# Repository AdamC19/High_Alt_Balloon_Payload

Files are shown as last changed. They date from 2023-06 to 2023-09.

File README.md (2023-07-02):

# High-Altitude Balloon Payload

These are the source files for my high-altitude balloon payload. 

Read more about this project and its development [on my website](http://acordingley.us/ke8itf/).

The primary goals of the payload are:
* Make measurements and collect data: 
    * GPS Location
    * Barometric pressure (second determination of altitude)
    * Temperature.
* Telemeter the data via the Amatuer Radio 2m band (144.39MHz).
* Log the data to non-volatile storage.
* Powered from NiMH batteries.

The primary goal of the real-time telemetry is to be able to receive GPS coordinates so that we can track the balloon and hopefully chase it and find it more easily. The payload will also include a self-contained camera to take pictures. 

## Hardware Block Diagrams
### Logical Overview
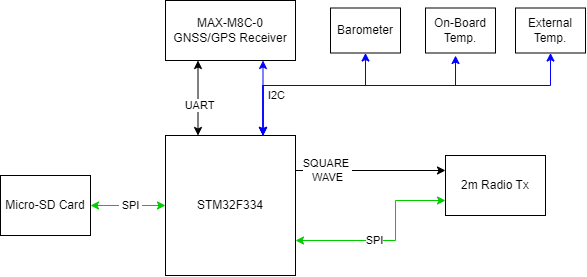
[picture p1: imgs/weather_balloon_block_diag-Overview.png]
High Altitude Balloon Payload Overview Block Diagram


### Power Architecture
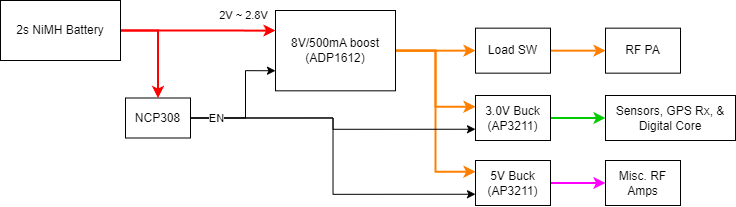
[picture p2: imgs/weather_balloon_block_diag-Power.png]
High Altitude Balloon Payload Power Block Diagram


### 2m Radio Transmitter
High Altitude Balloon Payload Radio Block Diagram

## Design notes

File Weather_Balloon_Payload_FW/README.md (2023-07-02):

# Payload Firmware

The boilerplate code was generated using STM32CubeMX. 

You can build using make, and it's convenient to use Visual Studio Code with the stm32-for-vscode extension.

## SD Card Driver

Big thanks to projects by kiwih for providing the boilerplate [SD card SPI driver code](https://01001000.xyz/2020-08-09-Tutorial-STM32CubeIDE-SD-card/).

The FAT filesystem middleware was provided by ST via STM32CubeMX.

You can configure the radio by including a file named `config.txt` on the SD card. I've included an example of such a file.

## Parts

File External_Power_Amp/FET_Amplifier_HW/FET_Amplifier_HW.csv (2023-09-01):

Source: | C:\Users\cordi\OneDrive\Documents\GitHub\Weather_Balloon\External_Power_Amp\FET_Amplifier_HW\FET_Amplifier_HW.kicad_sch
Date: | 7/29/2023 1:38:26 AM
Tool: | Eeschema 7.0.1
Generator: | C:\Program Files\KiCad\7.0\bin\scripting\plugins/bom_csv_grouped_by_value.py
Component Count: | 109
Collated Components:
Item | Qty | Reference(s) | Value | LibPart | Footprint | Datasheet | DNP | Current Rating | Description | JLCPCB Part # | MFG | MFG_PN | Manufacturer | Mfr Part # | Mfr. Part # | Package Desc | Tolerance | Voltage Rating
1 | 8 | C1, C5, C8, C16, C31, C39, C40, C41 | 1000pF | Device:C | Capacitor_SMD:C_0402_1005Metric | ~ |  |  | CAP SMD 1000pF 10% 50V X7R 0603 | C1588 |  |  | Samsung Electro-Mechanics | C1005NPO102JGT | CL10B102KB8NNNC | 0402 |  | 50V
2 | 1 | C2 | 5.6pF | Device:C | Capacitor_SMD:C_0402_1005Metric | ~ |  |  | CAP SMD 5.6pF 10% 50V NPO/C0G 0402 | C88895 |  |  | Murata Electronics |  | GJM1555C1H5R6CB01D | 0402 |  | 50V
3 | 1 | C3 | 12pF | Device:C | Capacitor_SMD:C_0402_1005Metric | ~ |  |  | CAP SMD 12pF 10% 50V NPO/C0G 0402 | C106201 |  |  | YAGEO |  | CC0402JRNPO9BN120 | 0402 |  | 50V
4 | 1 | C4 | 3.6pF | Device:C | Capacitor_SMD:C_0402_1005Metric | ~ | DNP |  | CAP SMD 3.6pF 10% 50V NPO/C0G 0402 | C161321 |  |  | Murata Electronics |  | GJM1555C1H3R6WB01D | 0402 |  | 50V
5 | 9 | C6, C7, C9, C15, C17, C20, C30, C33, C37 | 0.1uF | Device:C | Capacitor_SMD:C_0402_1005Metric | ~ |  |  | 50V 100nF X7R ±10% 0402 Multilayer Ceramic Capacitors MLCC - SMD/SMT ROHS | C77020 |  |  | Murata Electronics | GRM155R71H104KE14D | GRM155R71H104KE14D | 0402 |  | 50V
6 | 3 | C10, C14, C36 | 10uF | Device:C | Capacitor_SMD:C_1210_3225Metric | ~ |  |  | CAP SMD 10uF 50V 10% X7R 1210 | C386167 |  |  | Taiyo Yuden |  | UMK325AB7106KM-T | 1210 |  | 50V
7 | 2 | C11, C13 | 6.8pF | Device:C | Capacitor_SMD:C_0603_1608Metric | ~ |  |  | CAP SMD 6.8pF 10% 50V NP0/C0G 0603 | C1679 |  |  | FH (Guangdong Fenghua Advanced Tech) |  | 0603CG6R8C500NT | 0603 |  | 50V
8 | 2 | C12, C18 | 100pF | Device:C | Capacitor_SMD:C_0603_1608Metric | ~ |  |  | CAP SMD 100pF 10% 50V NP0/C0G 0603 | C14858 |  |  | Samsung Electro-Mechanics |  | CL10C101JB8NNNC | 0603 |  | 50V
9 | 1 | C19 | 0.022uF | Device:C | Capacitor_SMD:C_0402_1005Metric | ~ |  |  | CAP SMD 22nF 10% 50V X7R 0603 | C21122 |  |  | Samsung Electro-Mechanics |  | CL10B223KB8NNNC | 0402 |  | 50V
10 | 1 | C21 | 4.7uF | Device:C | Capacitor_SMD:C_0805_2012Metric | ~ |  |  | CAP CER 4.7UF 16V X5R 0805 | C1779 |  |  | Samsung Electro-Mechanics |  | CL21A475KAQNNNE | 0805 |  | 16V
11 | 1 | C22 | 1uF | Device:C | Capacitor_SMD:C_0805_2012Metric | ~ |  |  | CAP SMD 1uF 10% 50V X5R 0603 | C15849 |  |  | Samsung Electro-Mechanics |  | CL10A105KB8NNNC | 0805 |  | 50V
12 | 9 | C23, C25, C26, C27, C28, C29, C32, C34, C35 | 22uF | Device:C | Capacitor_SMD:C_1210_3225Metric | ~ |  |  | CAP CER 22uF 20% 25V X5R 1210 | C342660 |  |  | TDK |  | C3225X7R1C226KT000N | 1210 |  | 25V
13 | 1 | C24 | 1000pF | Device:C | Capacitor_SMD:C_0402_1005Metric | ~ | DNP |  | CAP SMD 1000pF 10% 50V X7R 0603 | C1588 |  |  | Samsung Electro-Mechanics | C1005NPO102JGT | CL10B102KB8NNNC | 0402 |  | 50V
14 | 1 | C38 | 2.2uF | Device:C | Capacitor_SMD:C_0603_1608Metric | ~ |  |  | 16V 2.2uF X7S ±10% 0603 Multilayer Ceramic Capacitors MLCC - SMD/SMT ROHS | C2859193 |  |  | SANYEAR |  | C0603X7S225K160NT | 0603 |  | 16V
15 | 1 | D1 | SS54SMA | Device:D_Schottky | Diode_SMD:D_SMA | ~ |  |  | 40V 550mV@3A 5A SMA Schottky | C511853 |  |  |  |  | SS54SMA
16 | 4 | FB1, FB2, FB3, FB4 | 330@100MHz | Device:L | Inductor_SMD:L_0603_1608Metric | ~ |  |  | 70mΩ ±25% 330Ω@100MHz 0603 Ferrite Beads ROHS | C710391 |  |  | Murata Electronics |  | BLM18SG331TZ1D
17 | 4 | H1, H2, H3, H4 | M2.5 | Mechanical:MountingHole_Pad | MountingHole:MountingHole_2.7mm_M2.5_Pad_Via | ~
18 | 2 | J1, J5 | Conn_Coaxial | Connector:Conn_Coaxial | Repowered_Connectors:SMA_Amphenol_132384_EdgeMount | ~
19 | 1 | J2 | Conn_01x02 | Connector_Generic:Conn_01x02 | Connector_PinHeader_2.54mm:PinHeader_1x02_P2.54mm_Vertical | ~
20 | 1 | J3 | JST-XH | Connector_Generic:Conn_01x02 | Connector_JST:JST_XH_B2B-XH-A_1x02_P2.50mm_Vertical | ~
21 | 1 | J4 | MM8430-2610 | Repowered_Devices:MM8430-2610 | Repowered_Connectors:Connector_Murata_MM8430-2610RA1 | https://media.digikey.com/pdf/Data%20Sheets/Murata%20PDFs/Microwave_Coaxial_Conn_Cat030E.pdf |  |  | CONN SWD RCPT W/ SWITCH 50 OHM SMD | C91634 | Murata | MM8430-2610RA1 | Murata |  | MM8430-2610RB3
22 | 1 | L1 | 18nH | Device:L | Inductor_SMD:L_0603_1608Metric | ~ |  |  |  | C1332655 |  |  |  |  | LQW18AN18NJ80D
23 | 1 | L2 | 16nH | Device:L | Inductor_SMD:L_0603_1608Metric | ~ |  |  |  | C237581 |  |  |  |  | LQW18AN16NG00D
24 | 3 | L3, L4, L6 | 180nH | Device:L | Repowered_Inductors_SMD:L_Coilcraft_2222SQ-181 | ~ |  |  |  |  |  |  |  |  | 2222SQ-181GEC
25 | 1 | L5 | 10nH | Device:L | Inductor_SMD:L_1008_2520Metric | ~ |  |  |  |  |  |  | Coilcraft |  | 1008CS-100XGLC
26 | 1 | L7 | 10uH | Device:L | Inductor_SMD:L_Sunlord_MWSA0624S | ~ |  | 3.1A (4A sat.) |  | C408435 |  |  | Sunlord |  | MWSA0624S-100MT
27 | 1 | L8 | 4.7uH | Device:L | Inductor_SMD:L_Sunlord_SWPA4018S | ~ |  |  |  | C60117 |  |  | Sunlord |  | SWPA4018S4R7MT
28 | 1 | L9 | 120nH | Device:L | Inductor_SMD:L_1008_2520Metric_Pad1.43x2.20mm_HandSolder | ~ |  |  |  | C703706 |  |  |  |  | LQW2UASR12G00L
29 | 1 | Q1 | BLP15H9S100GZ | Device:Q_NMOS_DGS | Repowered_TO-SOT-SMD:SOT-1483-1 | ~ |  |  |  |  |  |  | Ampleon USA Inc. |  | BLP15H9S100GZ
30 | 2 | Q2, Q5 | DMN3023L | Transistor_FET:DMG1012T | Repowered_TO-SOT-SMD:SOT-23 | https://www.diodes.com/assets/Datasheets/DMN3023L.pdf
31 | 1 | Q3 | Si2302 | Device:Q_NMOS_GSD | Repowered_TO-SOT-SMD:SOT-23 | ~ |  |  |  | C2891732 |  |  | YONGYUTAI |  | SI2302
32 | 1 | Q4 | DMP2035U-7 | Device:Q_PMOS_GSD | Repowered_TO-SOT-SMD:SOT-23 | ~ |  |  | MOSFET P-CH 20V 3.6A SOT23-3 | C443825 |  |  | Diodes Incorporated |  | DMP2035U-7
33 | 1 | R1 | 49.9 | Device:R_US | Resistor_SMD:R_0603_1608Metric | ~ |  |  | RES SMD 49.9 1% 100mW 0603 | C23185 |  |  | UNI-ROYAL(Uniroyal Elec) |  | 0603WAF499JT5E | 0603 | 1%
34 | 6 | R2, R10, R12, R14, R17, R21 | 0.0 | Device:R_US | Resistor_SMD:R_0603_1608Metric | ~ |  |  | 100mW ±1% 0Ω 0603 Chip Resistor - Surface Mount ROHS | C192909 |  |  | YAGEO |  | AF0603FR-070RL | 0603
35 | 2 | R3, R4 | 1.0 | Device:R_US | Resistor_SMD:R_0805_2012Metric | ~ |  |  |  | C144579 |  |  | YAGEO |  | AC0805FR-071RL | 0805 | 1%
36 | 2 | R5, R8 | 330 | Device:R_US | Resistor_SMD:R_0402_1005Metric | ~ |  |  |  | C25104 |  |  | UNI-ROYAL(Uniroyal Elec) |  | 0402WGF3300TCE | 0402 | 1%
37 | 1 | R6 | 1k | Device:R_US | Resistor_SMD:R_0402_1005Metric | ~ |  |  |  | C11702 |  |  | UNI-ROYAL(Uniroyal Elec) |  | 0402WGF1001TCE | 0402 | 1%
38 | 3 | R7, R11, R16 | 10k | Device:R_US | Resistor_SMD:R_0402_1005Metric | ~ |  |  | 62.5mW Thick Film Resistors ±0.5% 10.2kΩ 0402 Chip Resistor - Surface Mount ROHS | C303730 |  |  | RALEC |  | RTT021022DTH | 0402 | 1%
39 | 1 | R9 | 24.9k | Device:R_US | Resistor_SMD:R_0402_1005Metric | ~ |  |  |  | C138027 |  |  | YAGEO |  | RC0402FR-0724K9L | 0402 | 1%
40 | 2 | R13, R19 | 0.0 | Device:R_US | Resistor_SMD:R_0603_1608Metric | ~ | DNP |  | 100mW ±1% 0Ω 0603 Chip Resistor - Surface Mount ROHS | C192909 |  |  | YAGEO |  | AF0603FR-070RL | 0603
41 | 1 | R15 | 7.5k | Device:R_US | Resistor_SMD:R_0402_1005Metric | ~ |  |  |  | C25918 |  |  | UNI-ROYAL(Uniroyal Elec) |  | 0402WGF7501TCE | 0402 | 1%
42 | 1 | R18 | 0.005 | Device:R_US | Resistor_SMD:R_0805_2012Metric | ~ |  |  |  | C163091 |  |  | TA-I Tech |  | RLM10FTSMR005 | 0805 | 1%
43 | 1 | R20 | 100k | Device:R_US | Resistor_SMD:R_0402_1005Metric | ~ |  |  |  | C25741 |  |  | UNI-ROYAL(Uniroyal Elec) |  | 0402WGF1003TCE | 0402 | 1%
44 | 1 | R22 | 1.8 | Device:R_US | Resistor_SMD:R_0805_2012Metric | ~ |  |  |  | C384139 |  |  | Walsin Tech Corp |  | WR08X1R8JTL | 0805 | 1%
45 | 1 | RV1 | 10k | Device:R_Potentiometer_US | Potentiometer_SMD:Potentiometer_Bourns_3314G_Vertical | ~ |  |  |  | C780220 | Bourns | 3314G-1-103E | Bourns |  | 3314G-1-103E
46 | 13 | TP1, TP2, TP3, TP4, TP5, TP6, TP7, TP8, TP9, TP10, TP11, TP12, TP13 | TestPoint | Connector:TestPoint | TestPoint:TestPoint_Pad_D1.0mm | ~
47 | 1 | U1 | AP9101CK6 | Battery_Management:AP9101CK6 | Package_TO_SOT_SMD:SOT-23-6 | https://www.diodes.com/assets/Datasheets/AP9101C.pdf |  |  |  | C151339 |  |  |  |  | AP9101CK6-ADTRG1
48 | 1 | U2 | LT3759xMSE | Analog_Devices:LT3759 | Package_SO:MSOP-12-1EP_3x4mm_P0.65mm_EP1.65x2.85mm |  |  |  | IC, Mult. Topology Power Controller, Wide Vin |  |  | LT3759EMSE#TRPBF |  |  | LT3759EMSE#TRPBF
49 | 1 | U3 | AP63205WU-7 | Regulator_Switching:AP63205WU | Package_TO_SOT_SMD:TSOT-23-6 | https://www.diodes.com/assets/Datasheets/AP63200-AP63201-AP63203-AP63205.pdf |  |  |  | C2071056 |  |  |  |  | AP63205WU-7
50 | 1 | U4 | PGA-105 | RF_Amplifier:PGA-105 | Package_TO_SOT_SMD:SOT-89-3 | https://www.minicircuits.com/pdfs/PGA-105+.pdf |  |  |  | C879859 |  |  |  | PGA-105+

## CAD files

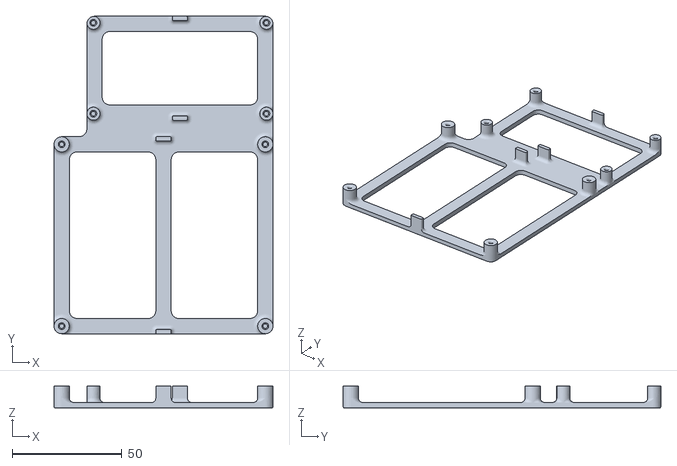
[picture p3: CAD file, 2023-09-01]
CAD/Main_Boards_Base.stl
100.0 x 145.0 x 10.0

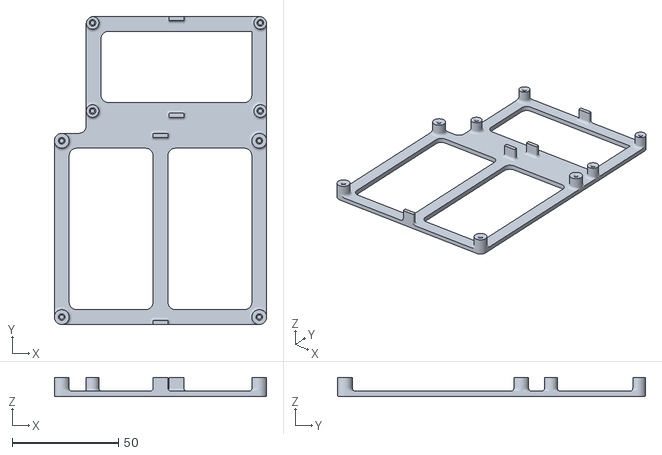
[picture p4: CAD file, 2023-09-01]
CAD/Main_Boards_Base v11.stl
100.0 x 145.0 x 9.00

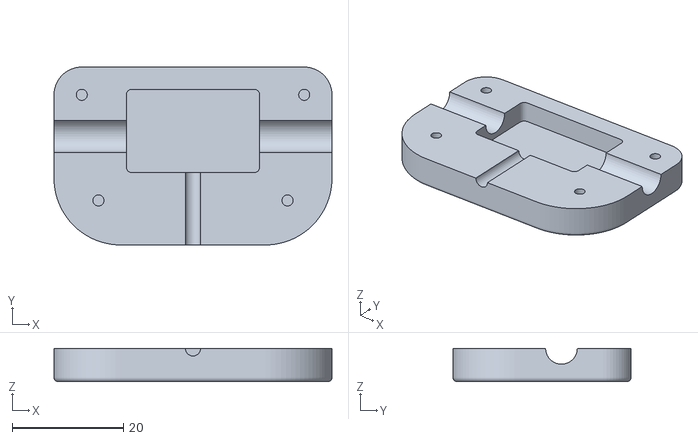
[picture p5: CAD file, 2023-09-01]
CAD/Dipole_Feedpoint_2m_bot.stl
50.0 x 32.0 x 6.00

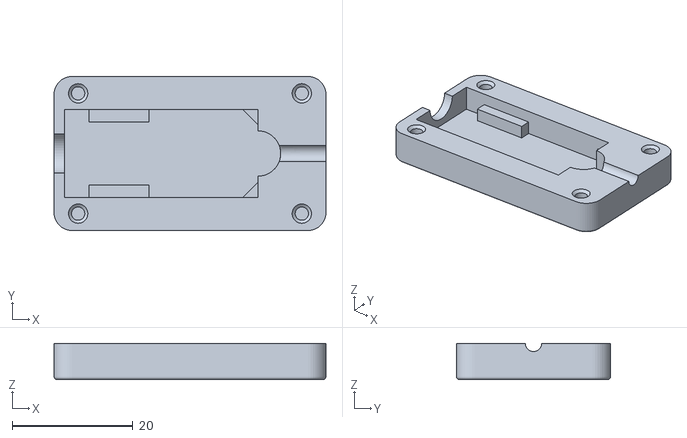
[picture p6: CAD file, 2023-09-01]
CAD/Imp_Match_Case_Bot.stl
45.0 x 25.5 x 6.00

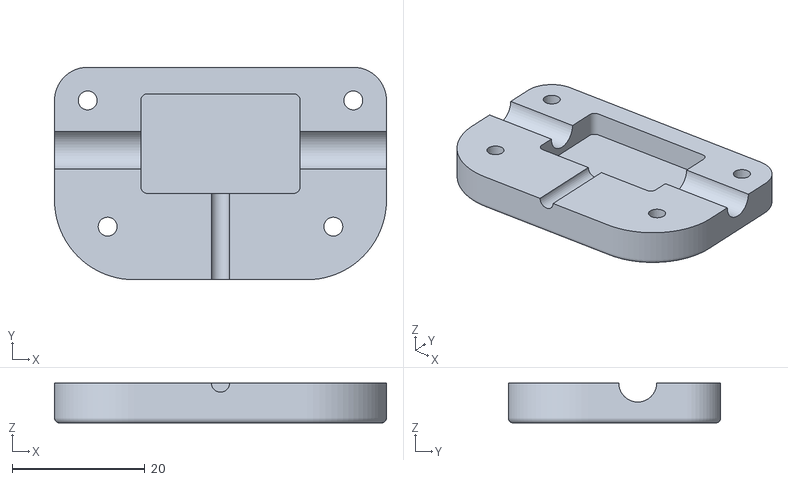
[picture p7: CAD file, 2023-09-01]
CAD/Dipole_Feedpoint_2m_top.stl
50.0 x 32.0 x 6.00

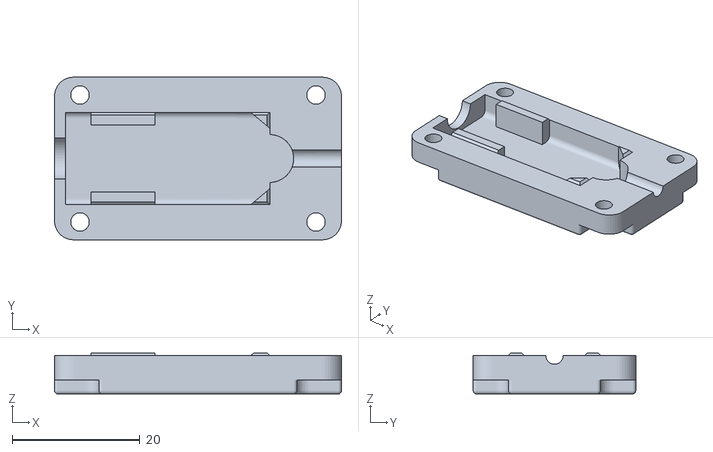
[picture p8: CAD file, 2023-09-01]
CAD/Imp_Match_Case_Top_rev2.stl
45.0 x 25.5 x 6.40

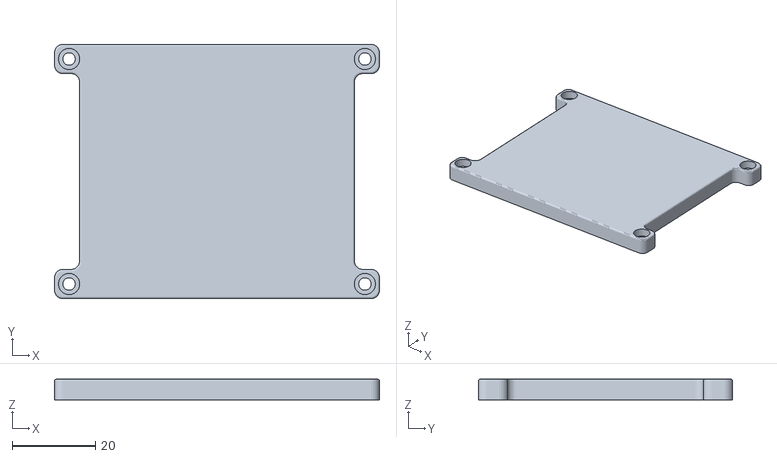
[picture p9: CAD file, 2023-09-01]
CAD/AA_battery_Case_2s2p_Bottom.stl
78.0 x 61.0 x 5.00

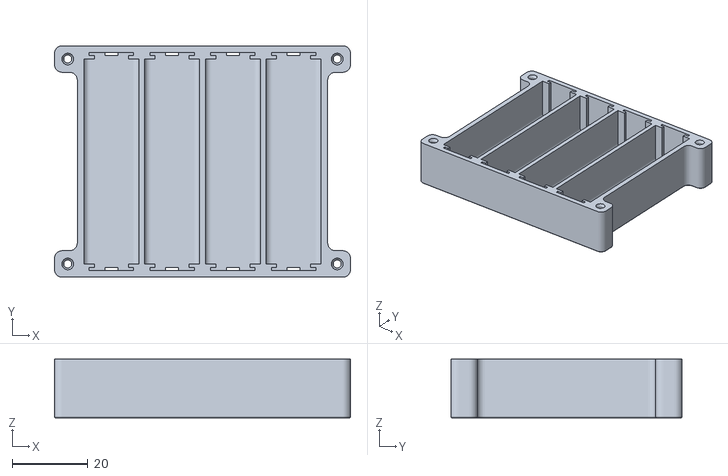
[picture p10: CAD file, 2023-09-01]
CAD/AA_Battery_Case_2s2p.stl
78.0 x 61.0 x 15.5

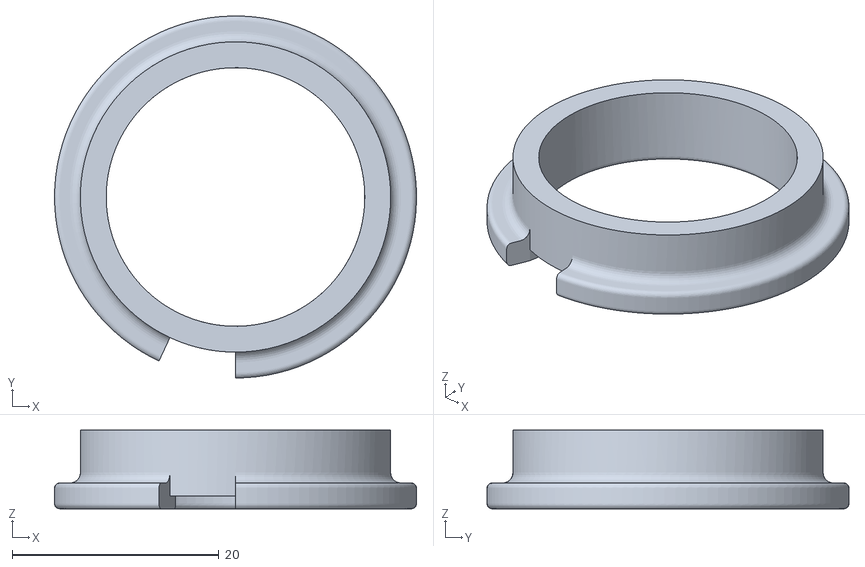
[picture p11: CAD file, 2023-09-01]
CAD/balun_bobbin.stl
35.0 x 35.0 x 7.60

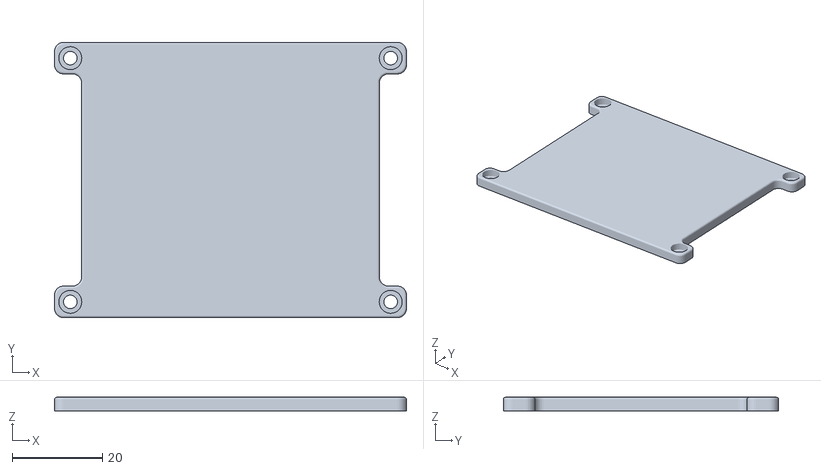
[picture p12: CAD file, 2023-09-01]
CAD/AA_battery_Case_2s2p_Top.stl
78.0 x 61.0 x 3.00

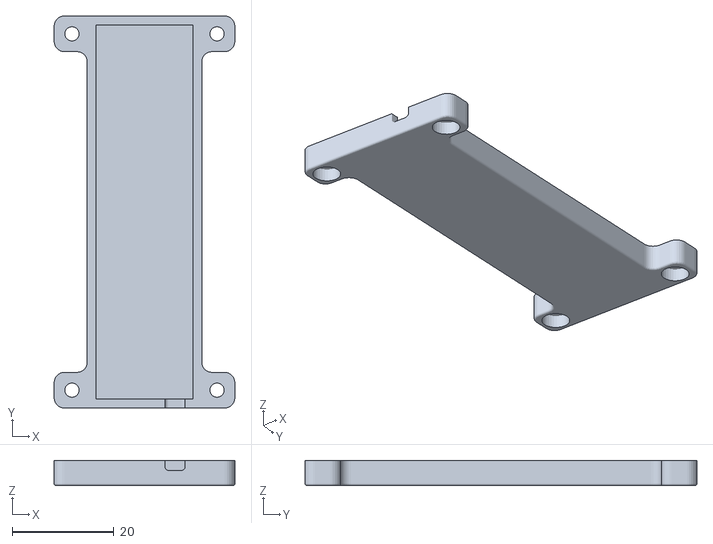
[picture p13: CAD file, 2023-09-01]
CAD/18650_battery_case_bottom.stl
35.5 x 77.0 x 5.00

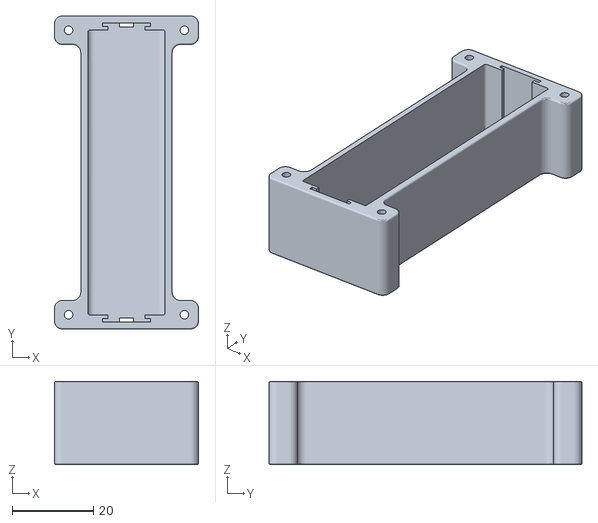
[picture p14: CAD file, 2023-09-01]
CAD/18650_Battery_Case_1s1p.stl
35.5 x 77.0 x 20.5

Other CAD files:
CAD/Imp_Match_Case_Top.stl

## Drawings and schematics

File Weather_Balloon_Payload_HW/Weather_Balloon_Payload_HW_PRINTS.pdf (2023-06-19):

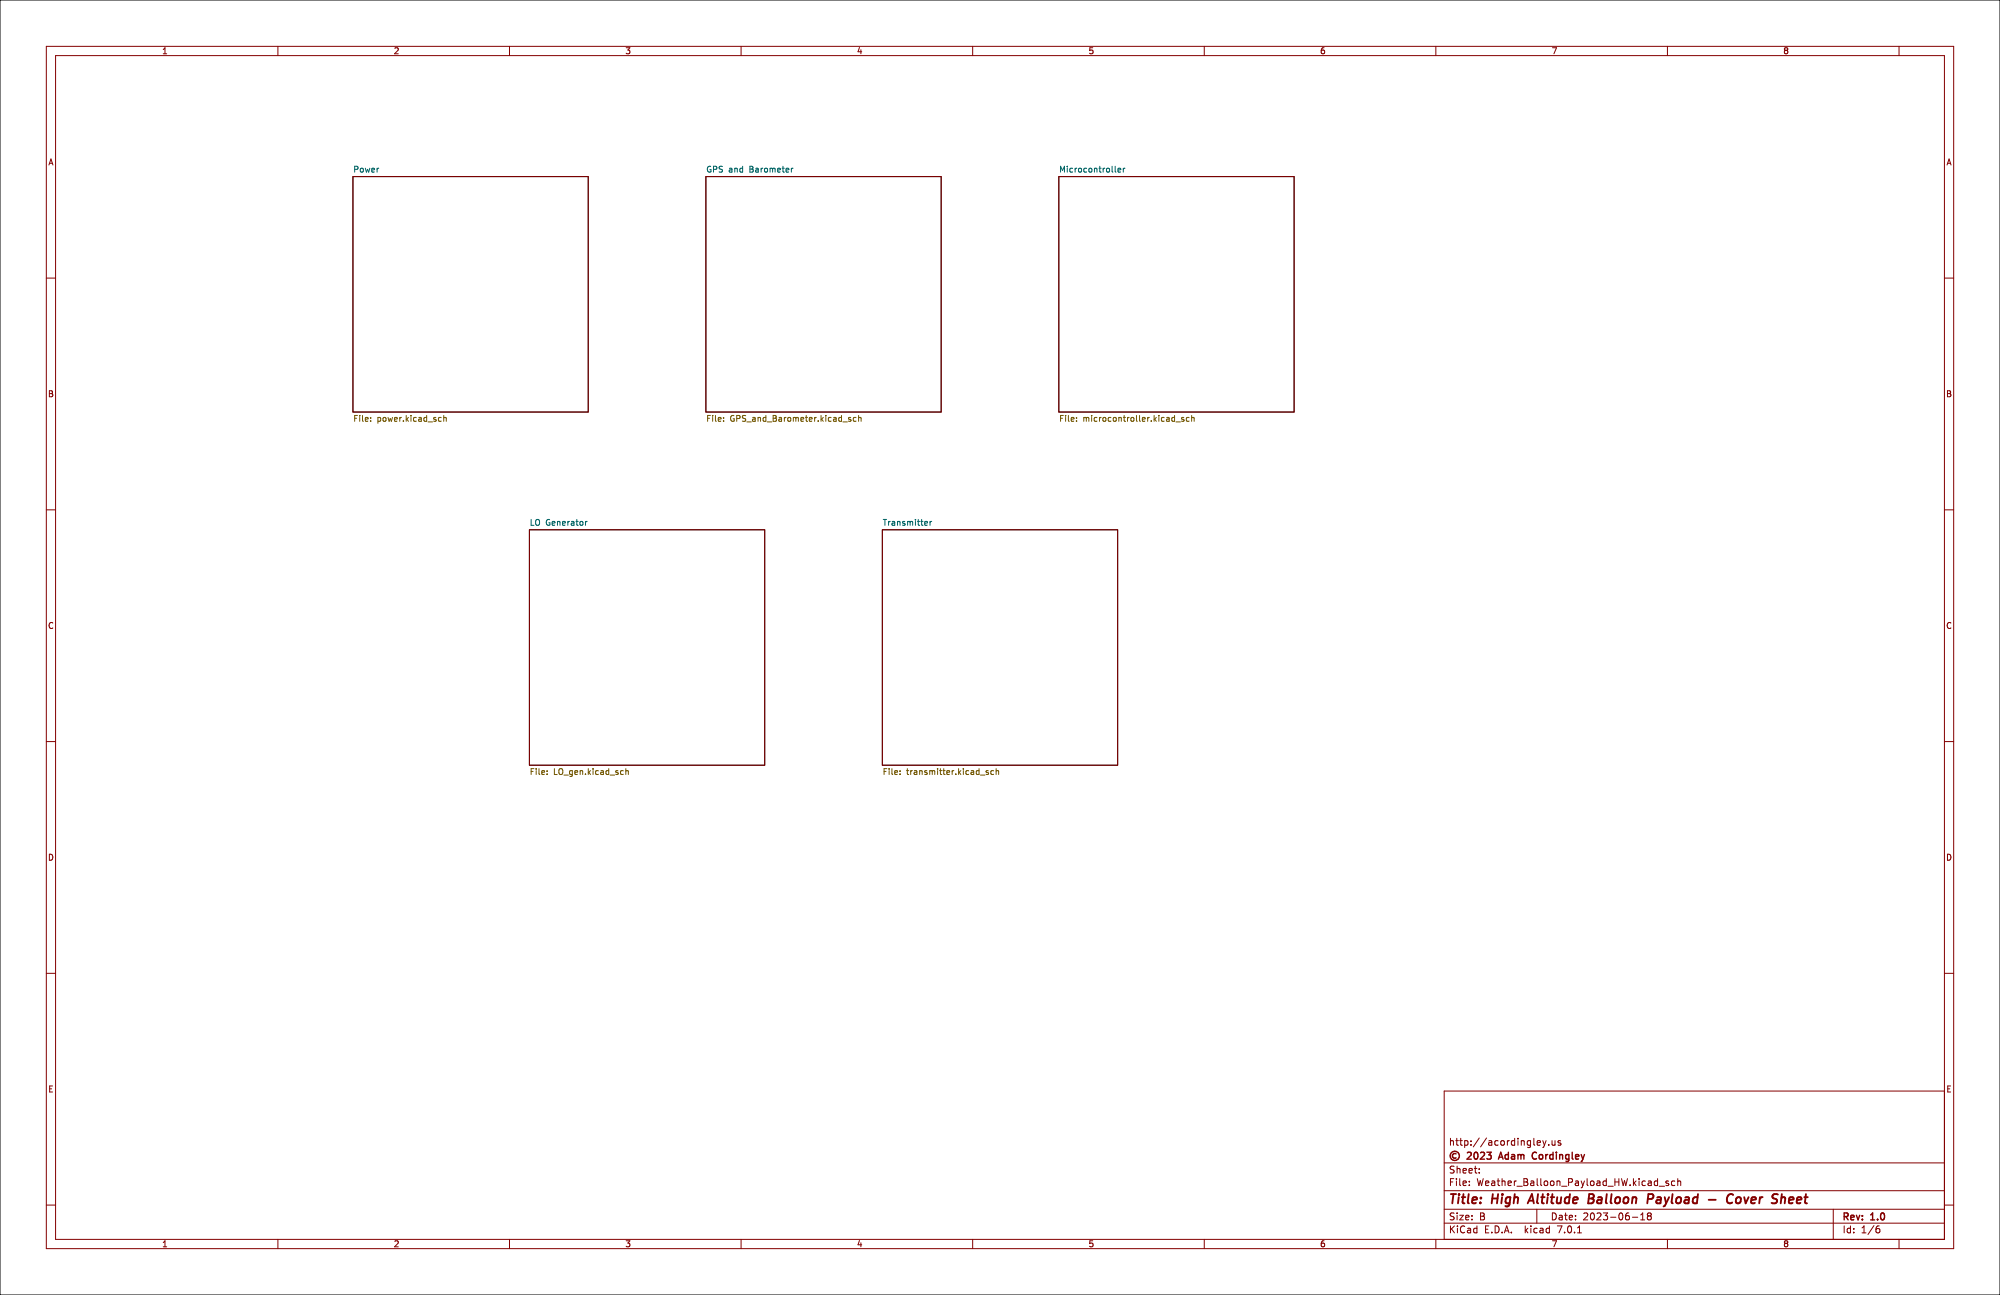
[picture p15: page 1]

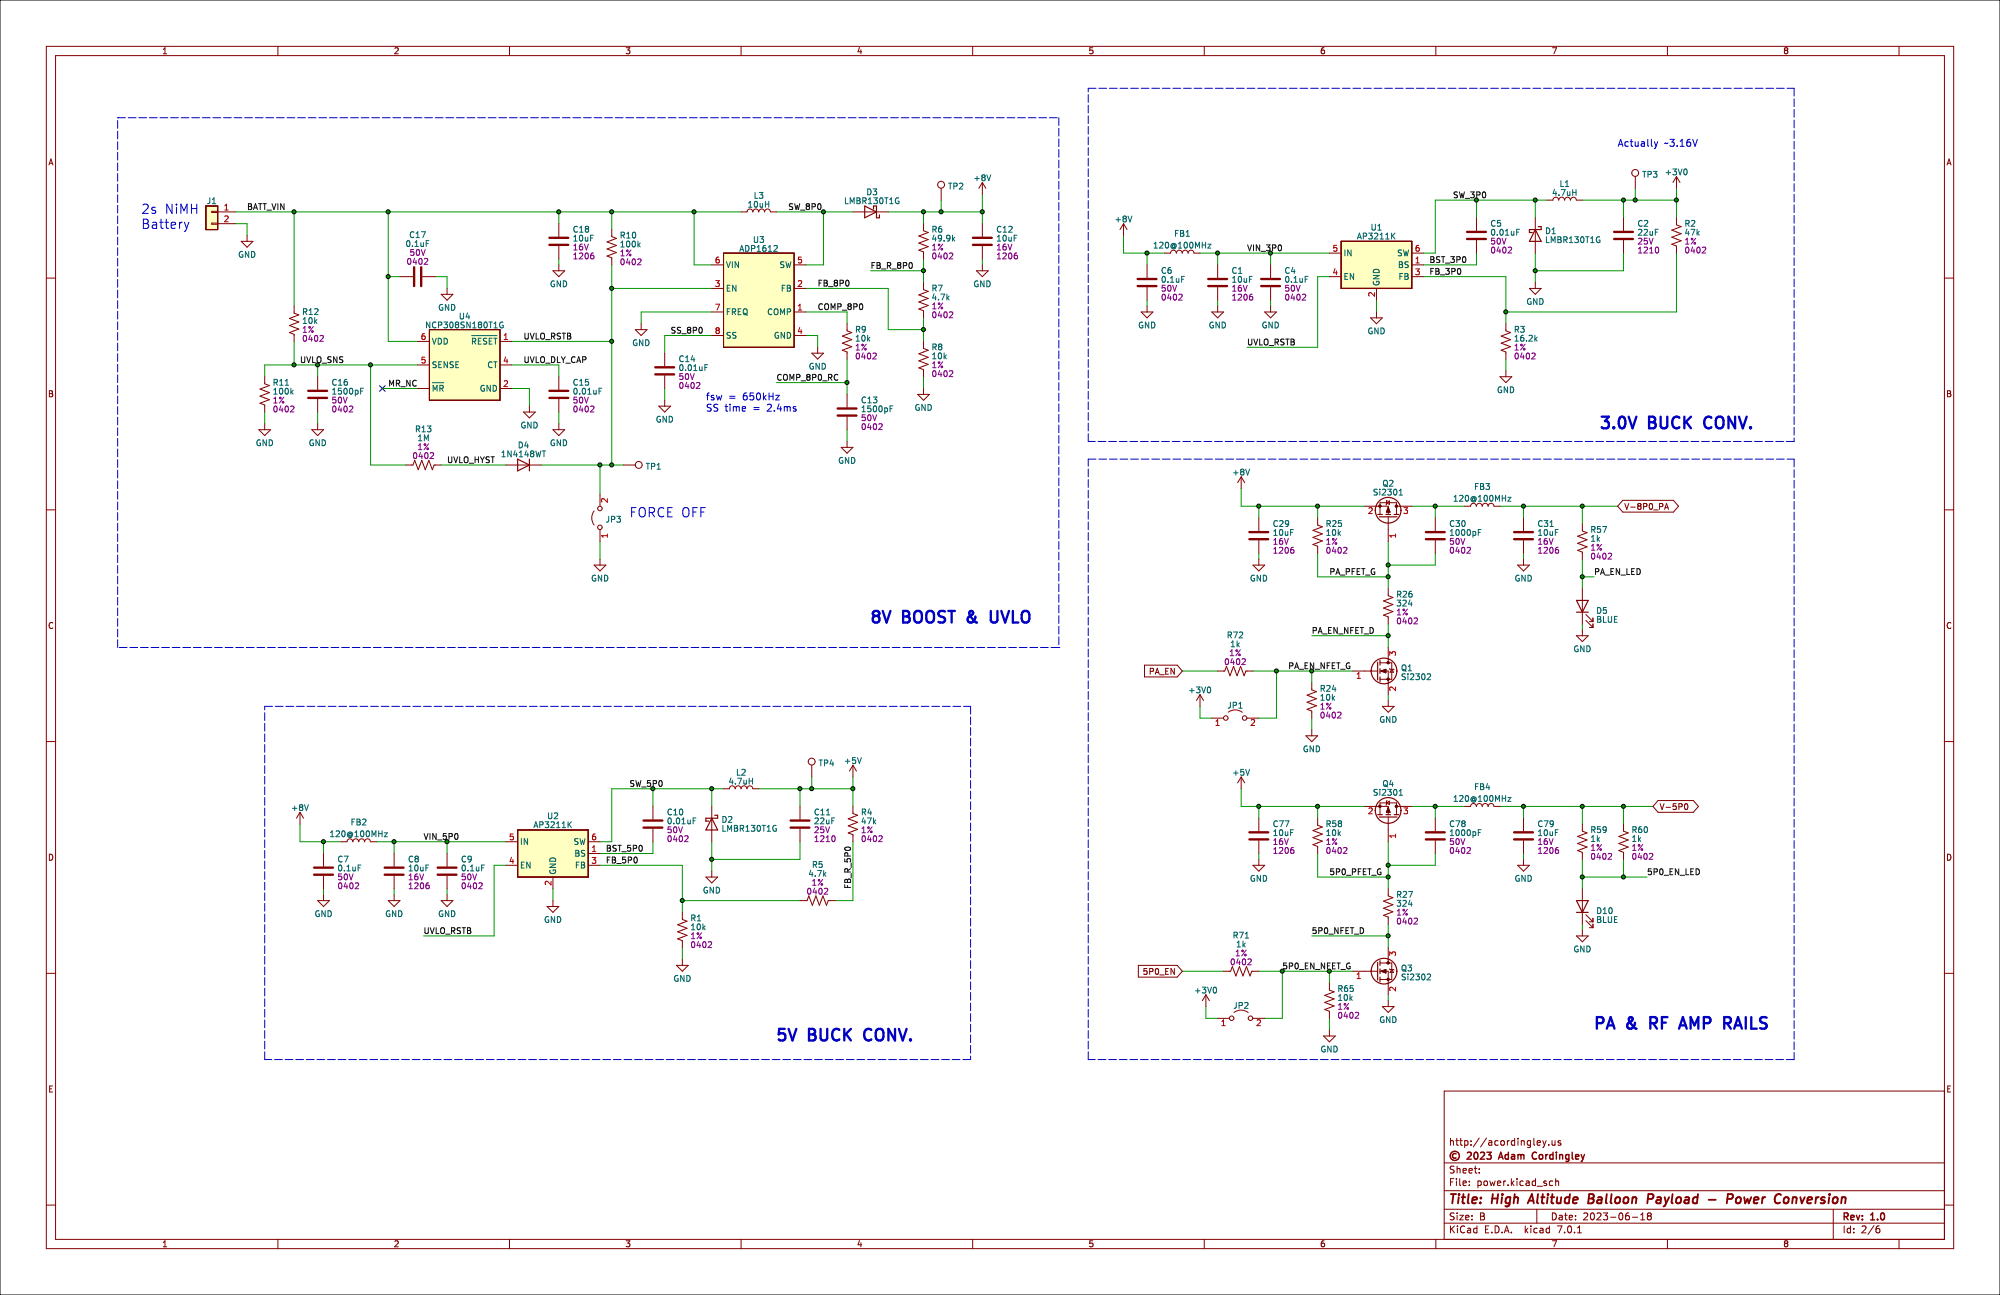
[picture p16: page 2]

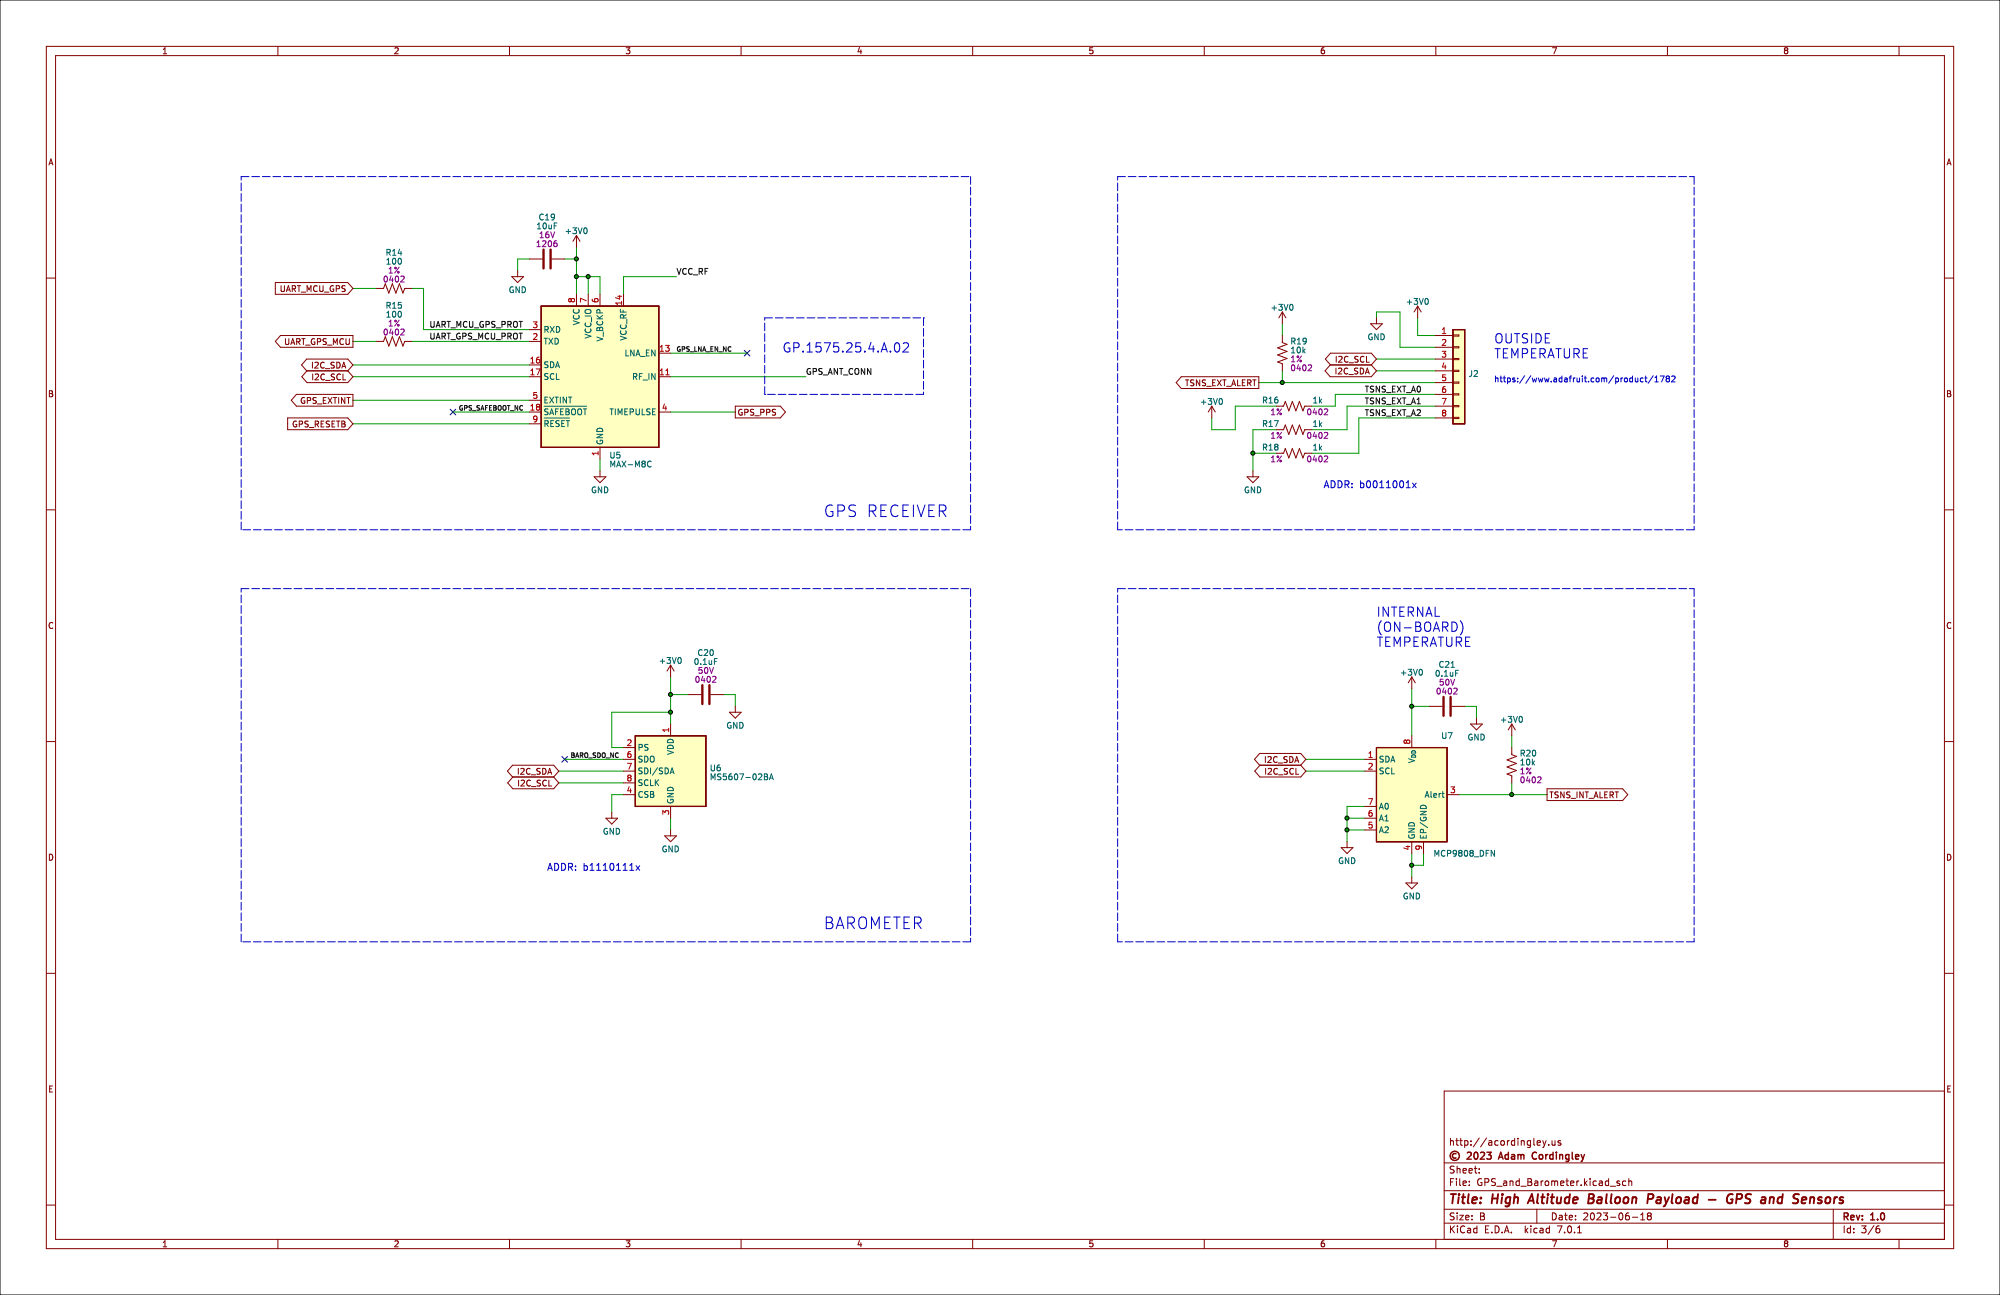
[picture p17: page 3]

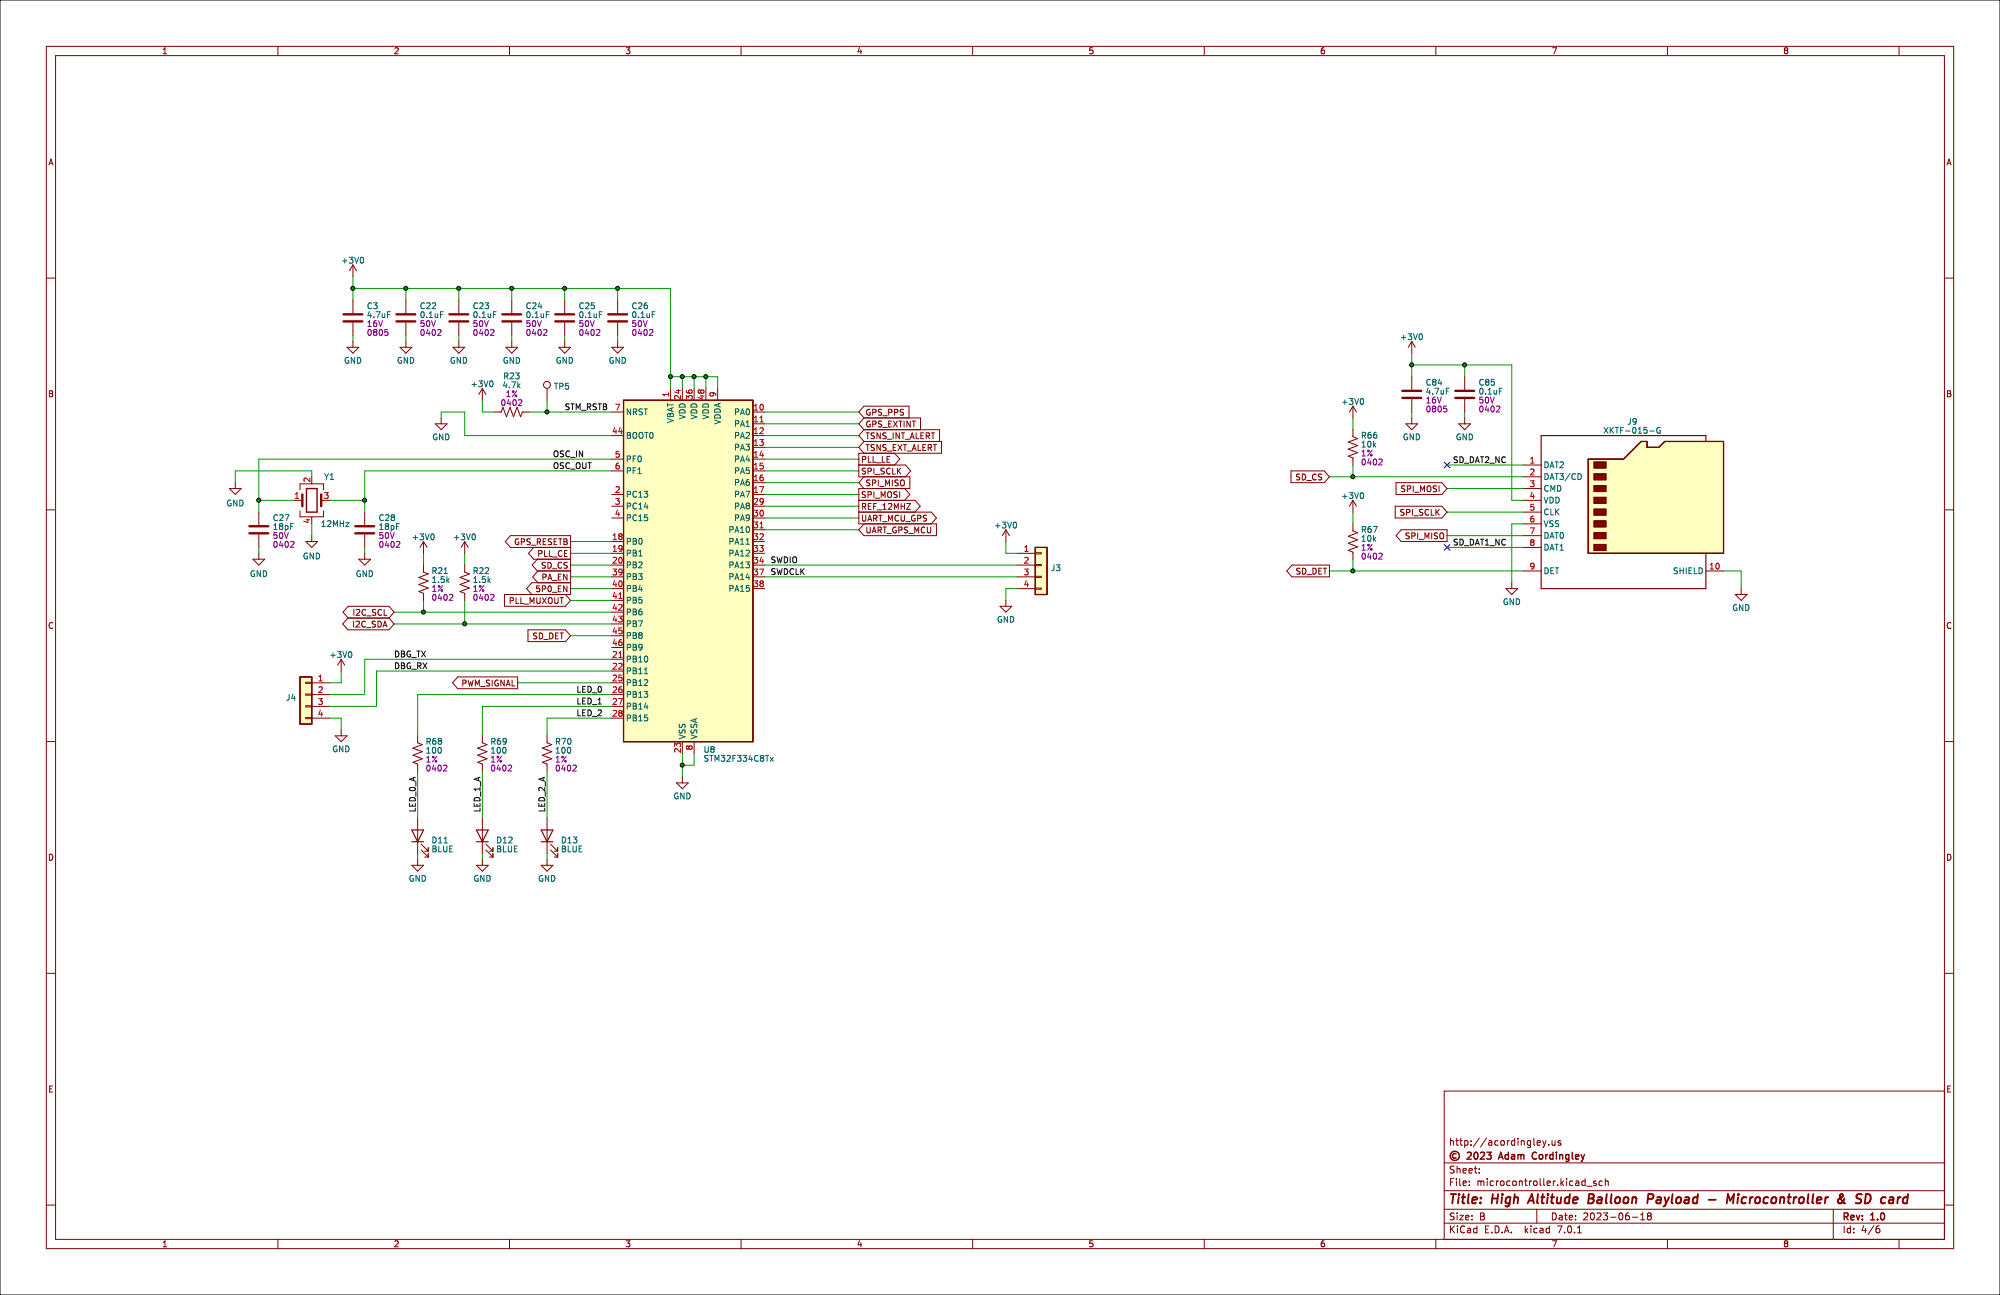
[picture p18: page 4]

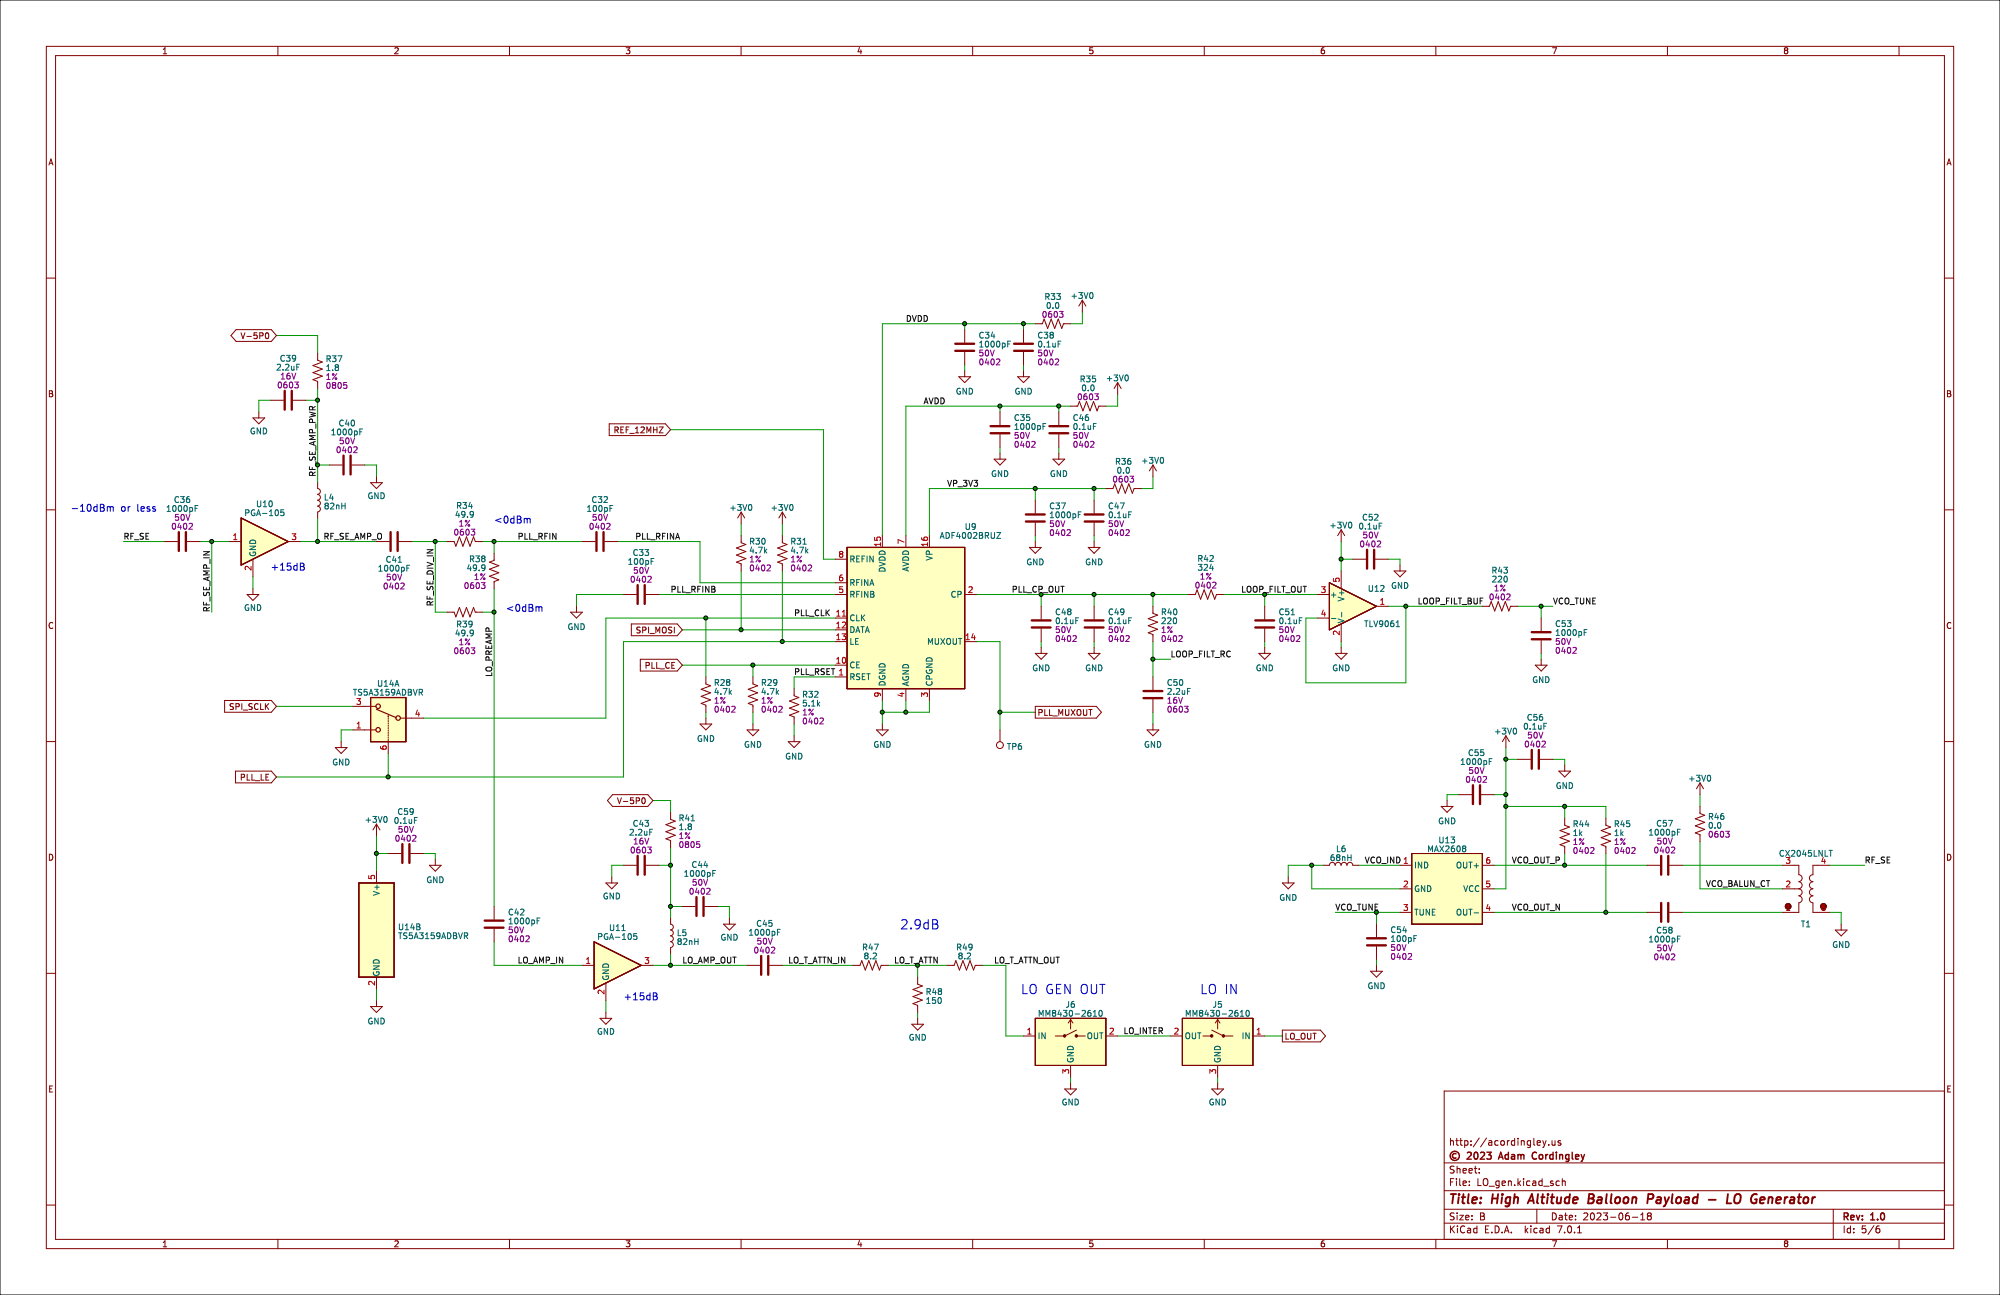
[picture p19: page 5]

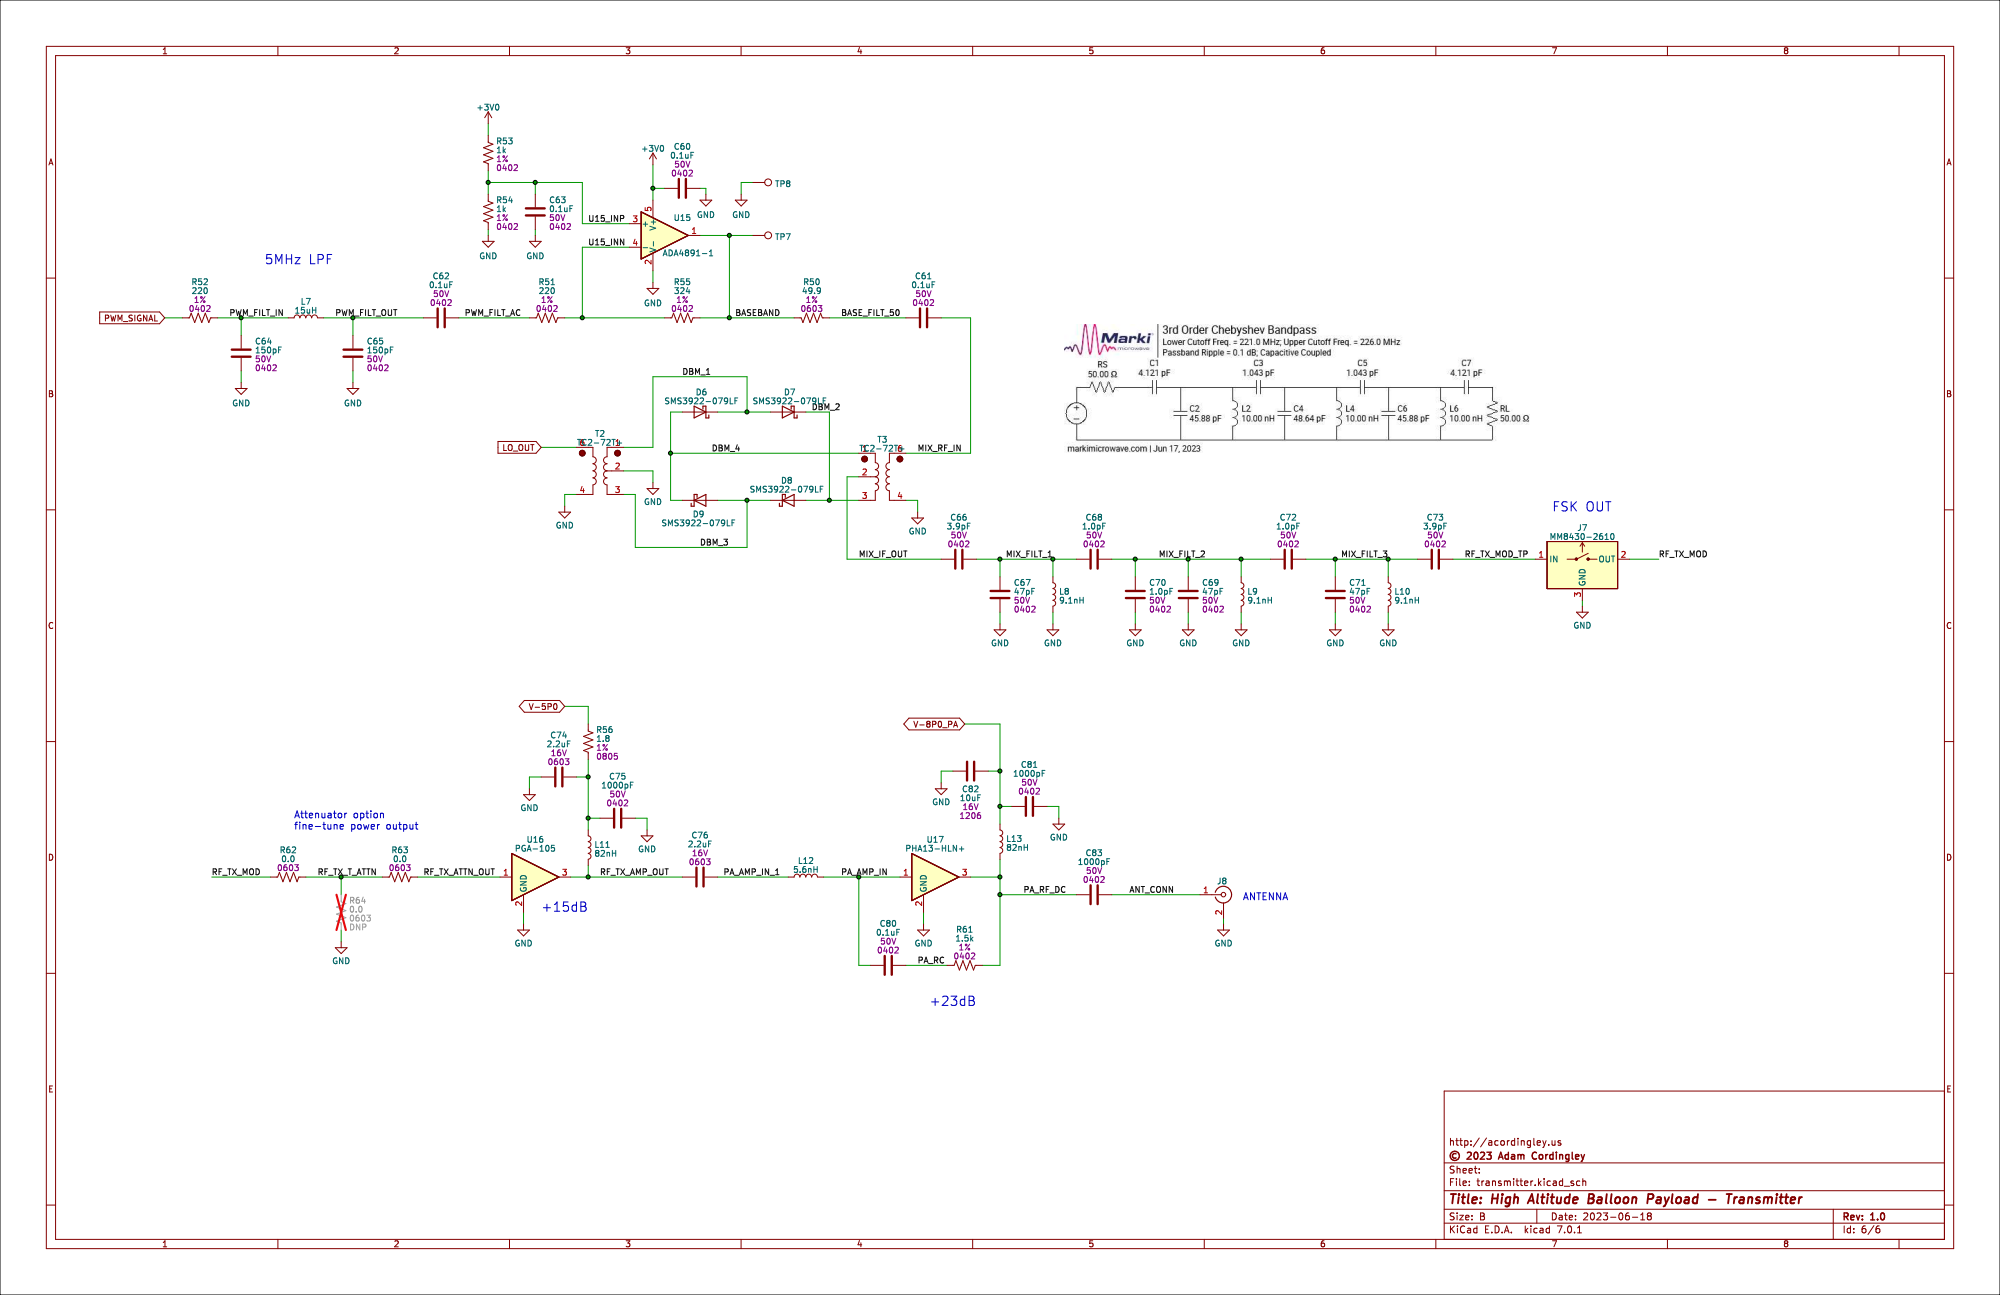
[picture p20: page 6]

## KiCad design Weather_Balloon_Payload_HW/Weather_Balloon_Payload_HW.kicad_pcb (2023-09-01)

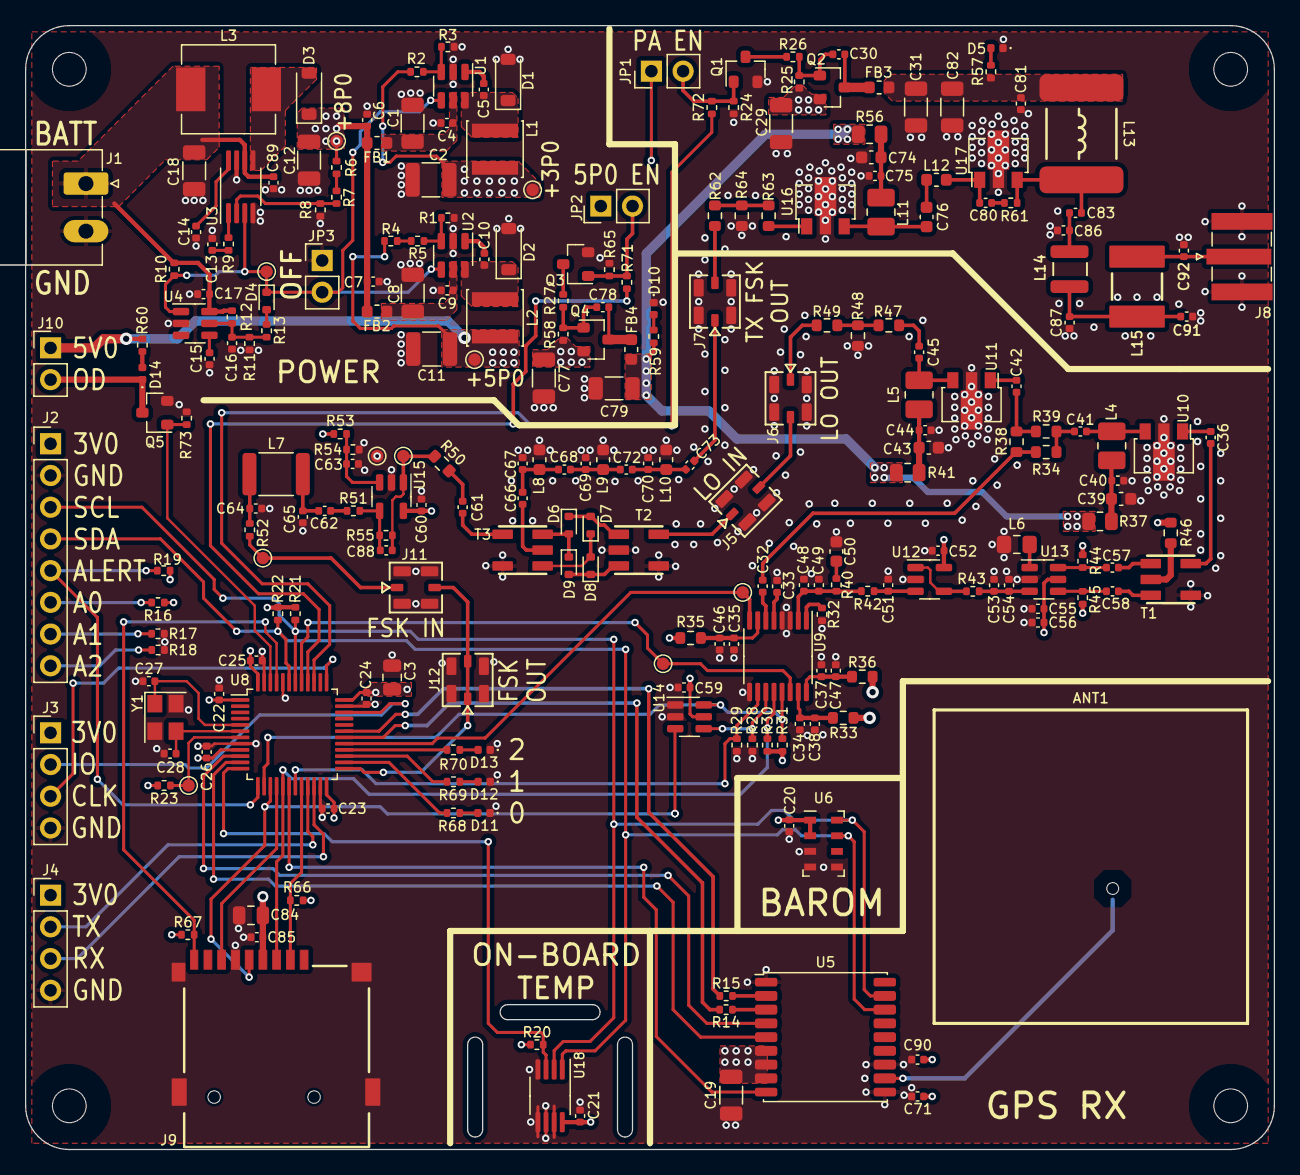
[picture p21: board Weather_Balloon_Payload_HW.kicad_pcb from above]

Board: 4 copper layers, 100.0 x 90.0 mm, 254 parts (0 on the bottom side), 142 nets.

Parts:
ANT1: GP.1575.25.4.A.02; Taoglas_GP.1575.25.4.A.02
C1, C8, C12, C18, C19, C29, C31, C77, C79, C82: 10uF; C_1206_3216Metric
C2, C11: 22uF; C_1210_3225Metric
C3, C84: 4.7uF; C_0805_2012Metric
C4, C6, C7, C9, C17, C20, C21, C22, C23, C24, C25, C26, C38, C46, C47, C48, C49, C51, C52, C56, C59, C60, C61, C62, C63, C80, C85, C89: 0.1uF; C_0402_1005Metric
C5, C10, C14, C15: 0.01uF; C_0402_1005Metric
C13, C16: 1500pF; C_0402_1005Metric
C27, C28, C91, C92: 18pF; C_0402_1005Metric
C30, C34, C35, C36, C37, C40, C41, C42, C44, C45, C53, C55, C57, C58, C71, C75, C78, C81, C83, C90: 1000pF; C_0402_1005Metric
C32, C33, C54, C88: 100pF; C_0402_1005Metric
C39, C43, C50, C74, C76: 2.2uF; C_0603_1608Metric
C64, C65: 150pF; C_0402_1005Metric
C66, C73: 12pF; C_0402_1005Metric
C67, C69, C70: 110pF; C_0402_1005Metric
C68, C72: 4.7pF; C_0402_1005Metric
C86, C87: 10pF; C_0402_1005Metric
D1, D2, D3: LMBR130T1G; D_SOD-123
D4: 1N4148WT; D_SOD-523
D5, D10, D11, D12, D13, D14: BLUE; LED_0402_1005Metric
D6, D7, D8, D9: SMS3922-079LF; D_SOD-523
FB1, FB2, FB3, FB4: 120@100MHz; L_0603_1608Metric
H1, H2, H3, H4: M2.5; MountingHole_2.7mm_M2.5
J1: Conn_01x02; PhoenixContact_MC_1,5_2-G-3.81_1x02_P3.81mm_Horizontal
J2: Conn_01x08; PinHeader_1x08_P2.54mm_Vertical
J3, J4: Conn_01x04; PinHeader_1x04_P2.54mm_Vertical
J5, J6, J7, J11, J12: MM8430-2610; Connector_Murata_MM8430-2610RA1
J8: Conn_Coaxial; SMA_Amphenol_132384_EdgeMount
J9: XKTF-015-G; microSD_Card_Socket_Generic
J10: Conn_01x02; PinHeader_1x02_P2.54mm_Vertical
JP1, JP2, JP3: Jumper_2_Open; PinHeader_1x02_P2.54mm_Vertical
L1, L2: 4.7uH; L_Sunlord_SWPA4018S
L3: 10uH; L_Sunlord_MWSA0624S
L4, L5, L11: 120nH; L_1008_2520Metric_Pad1.43x2.20mm_HandSolder
L6: 180nH; L_0805_2012Metric_Pad1.15x1.40mm_HandSolder
L7: 15uH; L_1812_4532Metric
L8, L9, L10: 9.1nH; L_0603_1608Metric
L12: 5.6nH; L_0603_1608Metric
L13: 180nH; L_Coilcraft_2222SQ-181
L14: 47nH; L_Coilcraft_1111SQ-47N
L15: 68nH; L_Coilcraft_1515SQ-68N
Q1, Q3, Q5: Si2302; SOT-23
Q2, Q4: Si2301; SOT-23
R1, R8, R9, R12, R19, R20, R24, R25, R58, R65, R66, R67, R73: 10k; R_0402_1005Metric
R2, R4: 47k; R_0402_1005Metric
R3: 16.2k; R_0402_1005Metric
R5, R7, R23, R28, R29, R30, R31: 4.7k; R_0402_1005Metric
R6: 49.9k; R_0402_1005Metric
R10, R11: 100k; R_0402_1005Metric
R13: 1M; R_0402_1005Metric
R14, R15, R68, R69, R70: 100; R_0402_1005Metric
R16, R17, R18, R44, R45, R53, R54, R57, R71, R72: 1k; R_0402_1005Metric
R21, R22, R61: 1.5k; R_0402_1005Metric
R26, R27, R42, R55: 324; R_0402_1005Metric
R32: 5.1k; R_0402_1005Metric
R33, R35, R36, R46, R62, R63, R64: 0.0; R_0603_1608Metric
R34, R38, R39, R50: 49.9; R_0603_1608Metric
R37, R41, R56: 1.8; R_0805_2012Metric
R40, R43, R51, R52: 220; R_0402_1005Metric
R47, R49: 8.2; R_0603_1608Metric
R48: 150; R_0603_1608Metric
R59, R60: 470; R_0402_1005Metric
T1: CX2045LNLT; XFMR_Pulse_CX2049LNLT
T2, T3: TC2-72T+; XFMR_Mini-Circuits_TC2-72T+
TP1, TP2, TP3, TP4, TP5, TP6, TP7, TP8, TP9, TP10: TestPoint; TestPoint_Pad_D1.0mm
U1, U2: AP3211K; SOT-23-6
U3: ADP1612; MSOP-8_3x3mm_P0.65mm
U4: NCP308SN180T1G; SOT-23-6
U5: MAX-M8C; ublox_MAX
U6: MS5607-02BA; LGA-8_3x5mm_P1.25mm
U8: STM32F334C8Tx; LQFP-48_7x7mm_P0.5mm
U9: ADF4002BRUZ; TSSOP-16_4.4x5mm_P0.65mm
U10, U11, U16: PGA-105; SOT-89-3
U12: TLV9061; TSOT-23-5
U13: MAX2606; SOT-23-6
U14: TS5A3159ADBVR; SOT-23-6
U15: ADA4891-1; TSOT-23-5
U17: PHA13-HLN+; SOT-89-3
U18: MCP9808_MSOP; MSOP-8_3x3mm_P0.65mm
Y1: 12MHz; Crystal_SMD_3225-4Pin_3.2x2.5mm

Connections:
5P0_EN: R71.1, U8.40 (PB4)
+3V0: C2.1, C3.1, C19.2, C20.2, C21.2, C22.1, C23.1, C24.1, C25.1, C26.1, C52.1, C55.2, C56.1, C59.1, C60.1, C71.2, C84.1, C85.1, C90.2, J2.1, J3.1, J4.1, J9.4 (VDD), JP1.1 (A), JP2.1 (A), L1.2, R2.2, R16.2, R19.1, R20.1, R21.2, R22.2, R23.2, R30.2, R31.2, R33.2, R35.2, R36.2, R44.1, R45.1, R46.2, R53.1, R66.1, R67.1, TP3.1, U5.6 (V_BCKP), U5.7 (VCC_IO), U5.8 (VCC), U6.1 (VDD), U6.2 (PS), U8.1 (VBAT), U8.9 (VDDA), U8.24 (VDD), U8.36 (VDD), U8.48 (VDD), U12.5 (V+), U13.5 (VCC), U14.5 (V+), U15.5 (V+), U18.8 (V_{DD})
+5V: C11.1, C77.1, J10.1, L2.2, Q4.2 (S), R4.2, R58.1, R60.1, TP4.1
+8V: C6.1, C7.1, C12.1, C29.1, D3.1 (K), FB1.1, FB2.1, Q2.2 (S), R6.1, R25.1, TP2.1
/GPS and Barometer/GPS_ANT_CONN: ANT1.1 (A), U5.11 (RF_IN)
/GPS and Barometer/TSNS_EXT_A0: J2.6, R16.1
/GPS and Barometer/TSNS_EXT_A1: J2.7, R17.1
/GPS and Barometer/TSNS_EXT_A2: J2.8, R18.1
/GPS and Barometer/UART_GPS_MCU_PROT: R15.2, U5.2 (TXD)
/GPS and Barometer/UART_MCU_GPS_PROT: R14.2, U5.3 (RXD)
/LO Generator/AVDD: C35.2, C46.1, R35.1, U9.7 (AVDD)
/LO Generator/DVDD: C34.2, C38.1, R33.1, U9.15 (DVDD)
/LO Generator/LOOP_FILT_BUF: R43.2, U12.1, U12.4 (-)
/LO Generator/LOOP_FILT_OUT: C51.1, R42.1, U12.3 (+)
/LO Generator/LOOP_FILT_RC: C50.1, R40.1
/LO Generator/LO_AMP_IN: C42.1, U11.1
/LO Generator/LO_AMP_OUT: C45.2, L5.2, U11.3
/LO Generator/LO_INTER: J5.2 (OUT), J6.2 (OUT)
/LO Generator/LO_PREAMP: C42.2, R38.2, R39.1
/LO Generator/LO_T_ATTN: R47.2, R48.2, R49.1
/LO Generator/LO_T_ATTN_IN: C45.1, R47.1
/LO Generator/LO_T_ATTN_OUT: J6.1 (IN), R49.2
/LO Generator/PLL_CLK: R28.2, U9.11 (CLK), U14.4
/LO Generator/PLL_CP_OUT: C48.1, C49.1, R40.2, R42.2, U9.2 (CP)
/LO Generator/PLL_RFIN: C32.2, R34.1, R38.1
/LO Generator/PLL_RFINA: C32.1, U9.6 (RFINA)
/LO Generator/PLL_RFINB: C33.1, U9.5 (RFINB)
/LO Generator/PLL_RSET: R32.1, U9.1 (RSET)
/LO Generator/RF_SE: C36.2, T1.4
/LO Generator/RF_SE_AMP_IN: C36.1, U10.1
/LO Generator/RF_SE_AMP_O: C41.2, L4.2, U10.3
/LO Generator/RF_SE_AMP_PWR: C39.1, C40.2, L4.1, R37.1
/LO Generator/RF_SE_DIV_IN: C41.1, R34.2, R39.2
/LO Generator/VCO_BALUN_CT: R46.1, T1.2
/LO Generator/VCO_IND: L6.2, U13.1 (IND)
/LO Generator/VCO_OUT_N: C58.1, R45.2, U13.4 (OUT-)
/LO Generator/VCO_OUT_P: C57.1, R44.2, U13.6 (OUT+)
/LO Generator/VCO_TUNE: C53.1, C54.1, R43.1, U13.3 (TUNE)
/LO Generator/VP_3V3: C37.2, C47.1, R36.1, U9.16 (VP)
/Microcontroller/BUZZ_LED_LOW: D14.1 (K), J10.2, Q5.3 (D)
/Microcontroller/BUZZ_LED_R: D14.2 (A), R60.2
/Microcontroller/DBG_RX: J4.3, U8.22 (PB11)
/Microcontroller/DBG_TX: J4.2, U8.21 (PB10)
/Microcontroller/HRTIM_CHC1: J11.2 (OUT), J12.1 (IN), J12.2 (OUT), U8.25 (PB12)
/Microcontroller/LED_0: R68.2, U8.26 (PB13)
/Microcontroller/LED_0_A: D11.2 (A), R68.1
/Microcontroller/LED_1: R69.2, U8.27 (PB14)
/Microcontroller/LED_1_A: D12.2 (A), R69.1
/Microcontroller/LED_2: R70.2, U8.28 (PB15)
/Microcontroller/LED_2_A: D13.2 (A), R70.1
/Microcontroller/OSC_IN: C27.2, U8.5 (PF0), Y1.1
/Microcontroller/OSC_OUT: C28.2, U8.6 (PF1), Y1.3
/Microcontroller/STM_RSTB: R23.1, TP5.1, U8.7 (NRST)
/Microcontroller/SWDCLK: J3.3, U8.37 (PA14)
/Microcontroller/SWDIO: J3.2, U8.34 (PA13)
/Power/5P0_EN_LED: D10.2 (A), R59.2
/Power/5P0_EN_NFET_G: JP2.2 (B), Q3.1 (G), R65.1, R71.2
/Power/5P0_NFET_D: Q3.3 (D), R27.2
/Power/5P0_PFET_G: C78.1, Q4.1 (G), R27.1, R58.2
/Power/BATT_VIN: C17.1, C18.1, C89.2, J1.1, L3.1, R10.2, R12.1, U3.6 (VIN), U4.6 (VDD)
/Power/BST_3P0: C5.2, U1.1 (BS)
/Power/BST_5P0: C10.2, U2.1 (BS)
/Power/COMP_8P0: R9.1, U3.1 (COMP)
/Power/COMP_8P0_RC: C13.1, R9.2
/Power/FB_3P0: R2.1, R3.1, U1.3 (FB)
/Power/FB_5P0: R1.1, R5.2, U2.3 (FB)
/Power/FB_8P0: R7.1, R8.1, U3.2 (FB)
/Power/FB_R_5P0: R4.1, R5.1
/Power/FB_R_8P0: R6.2, R7.2
/Power/PA_EN_LED: D5.2 (A), R57.2
/Power/PA_EN_NFET_D: Q1.3 (D), R26.2
/Power/PA_EN_NFET_G: JP1.2 (B), Q1.1 (G), R24.1, R72.2
/Power/PA_PFET_G: C30.1, Q2.1 (G), R25.2, R26.1
/Power/SS_8P0: C14.1, U3.8 (SS)
/Power/SW_3P0: C5.1, D1.1 (K), L1.1, U1.6 (SW)
/Power/SW_5P0: C10.1, D2.1 (K), L2.1, U2.6 (SW)
/Power/SW_8P0: D3.2 (A), L3.2, U3.5 (SW)
/Power/SW_OUT_5P0: C78.2, FB4.1, Q4.3 (D)
/Power/SW_OUT_8P0: C30.2, FB3.1, Q2.3 (D)
/Power/UVLO_DLY_CAP: C15.1, U4.4 (CT)
/Power/UVLO_HYST: D4.2 (A), R13.2
/Power/UVLO_RSTB: D4.1 (K), JP3.2 (B), R10.1, TP1.1, U1.4 (EN), U2.4 (EN), U3.3 (EN), U4.1 (~RESET)
/Power/UVLO_SNS: C16.1, R11.2, R12.2, R13.1, U4.5 (SENSE)
/Power/VIN_3P0: C1.1, C4.1, FB1.2, U1.5 (IN)
/Power/VIN_5P0: C8.1, C9.1, FB2.2, U2.5 (IN)
/Transmitter/ANT_CONN: C92.2, J8.1 (In), L15.2
/Transmitter/ANT_MATCH: C83.1, C86.1, L14.1
/Transmitter/ANT_MATCH_2: C87.1, C91.2, L14.2, L15.1
/Transmitter/BASEBAND: C88.2, R50.2, R55.1, TP7.1, U15.1
/Transmitter/BASE_FILT_50: C61.1, R50.1
/Transmitter/DBM_1: D6.1 (K), D7.2 (A), T2.3
/Transmitter/DBM_2: D7.1 (K), D8.2 (A), T3.3
/Transmitter/DBM_3: D8.1 (K), D9.2 (A), T2.1
/Transmitter/DBM_4: D6.2 (A), D9.1 (K), T3.1
/Transmitter/MIX_FILT_1: C66.1, C67.1, C68.2, L8.1
/Transmitter/MIX_FILT_2: C68.1, C69.1, C72.2, L9.1
/Transmitter/MIX_FILT_3: C70.1, C72.1, C73.2, L10.1
/Transmitter/MIX_IF_OUT: C66.2, T3.2
/Transmitter/MIX_RF_IN: C61.2, T3.6
/Transmitter/PA_AMP_IN: C80.1, L12.2, U17.1
/Transmitter/PA_AMP_IN_1: C76.1, L12.1
/Transmitter/PA_RC: C80.2, R61.2
/Transmitter/PA_RF_DC: C83.2, L13.2, R61.1, U17.3
/Transmitter/PWM_FILT_AC: C62.2, R51.2
/Transmitter/PWM_FILT_IN: C64.2, L7.1, R52.1
/Transmitter/PWM_FILT_OUT: C62.1, C65.2, L7.2
/Transmitter/RF_TX_AMP_OUT: C76.2, L11.2, U16.3
/Transmitter/RF_TX_ATTN_OUT: R63.2, U16.1
/Transmitter/RF_TX_MOD: J7.2 (OUT), R62.1
/Transmitter/RF_TX_MOD_TP: C73.1, J7.1 (IN)
/Transmitter/RF_TX_T_ATTN: R62.2, R63.1, R64.2
/Transmitter/U15_INN: C88.1, R51.1, R55.2, U15.4 (-)
/Transmitter/U15_INP: C63.2, R53.2, R54.1, U15.3 (+)
BUZZ_LED_EN: Q5.1 (G), R73.1, U8.46 (PB9)
GND: C1.2, C2.2, C3.2, C4.2, C6.2, C7.2, C8.2, C9.2, C11.2, C12.2, C13.2, C14.2, C15.2, C16.2, C17.2, C18.2, C19.1, C20.1, C21.1, C22.2, C23.2, C24.2, C25.2, C26.2, C27.1, C28.1, C29.2, C31.2, C33.2, C34.1, C35.1, C37.1, C38.2, C39.2, C40.1, C43.2, C44.1, C46.2, C47.2, C48.2, C49.2, C50.2, C51.2, C52.2, C53.2, C54.2, C55.1, C56.2, C59.2, C60.2, C63.1, C64.1, C65.1, C67.2, C69.2, C70.2, C71.1, C74.2, C75.1, C77.2, C79.2, C81.1, C82.2, C84.2, C85.2, C86.2, C87.2, C89.1, C90.1, C91.1, C92.1, D1.2 (A), D2.2 (A), D5.1 (K), D10.1 (K), D11.1 (K), D12.1 (K), D13.1 (K), J1.2, J2.2, J3.4, J4.4, J5.3 (GND), J6.3 (GND), J7.3 (GND), J8.2 (Ext), J9.6 (VSS), J9.10 (SHIELD), J11.3 (GND), J12.3 (GND), JP3.1 (A), L6.1, L8.2, L9.2, L10.2, Q1.2 (S), Q3.2 (S), Q5.2 (S), R1.2, R3.2, R8.2, R11.1, R17.2, R18.2, R24.2, R28.1, R29.1, R32.2, R48.1, R54.2, R64.1, R65.2, R73.2, T1.6, T2.2, T2.6, T3.4, TP8.1, U1.2 (GND), U2.2 (GND), U3.4 (GND), U3.7 (FREQ), U4.2 (GND), U5.1 (GND), U5.10 (GND), U5.12 (GND), U6.3 (GND), U6.4 (CSB), U6.5 (CSB), U8.8 (VSSA), U8.23 (VSS), U8.35 (VSS), U8.44 (BOOT0), U8.47 (VSS), U9.3 (CPGND), U9.4 (AGND), U9.9 (DGND), U10.2 (GND), U11.2 (GND), U12.2 (V-), U13.2 (GND), U14.1, U14.2 (GND), U15.2 (V-), U16.2 (GND), U17.2 (GND), U18.4 (GND), U18.5 (A2), U18.6 (A1), U18.7 (A0), Y1.2, Y1.4
GPS_EXTINT: U5.5 (EXTINT), U8.11 (PA1)
GPS_PPS: U5.4 (TIMEPULSE), U8.10 (PA0)
GPS_RESETB: U5.9 (~RESET), U8.18 (PB0)
I2C_SCL: J2.3, R21.1, U5.17 (SCL), U6.8 (SCLK), U8.42 (PB6), U18.2 (SCL)
I2C_SDA: J2.4, R22.1, U5.16 (SDA), U6.7 (SDI/SDA), U8.43 (PB7), U18.1 (SDA)
LO_OUT: J5.1 (IN), T2.4
unnamed: C43.1, C44.2, L5.1, R41.1
unnamed: C57.2, T1.3
unnamed: C58.2, T1.1
unnamed: C74.1, C75.2, L11.1, R56.1
PA_EN: R72.1, U8.39 (PB3)
PLL_CE: R29.2, U8.19 (PB1), U9.10 (CE)
PLL_LE: R31.1, U8.14 (PA4), U9.13 (LE), U14.6
PLL_MUXOUT: TP6.1, U8.41 (PB5), U9.14 (MUXOUT)
PWM_SIGNAL: J11.1 (IN), R52.2, TP10.1
REF_12MHZ: TP9.1, U8.29 (PA8), U9.8 (REFIN)
SD_CS: J9.2 (DAT3/CD), R66.2, U8.20 (PB2)
SD_DET: J9.9 (DET), R67.2, U8.45 (PB8)
SPI_MISO: J9.7 (DAT0), U8.16 (PA6)
SPI_MOSI: J9.3 (CMD), R30.1, U8.17 (PA7), U9.12 (DATA)
SPI_SCLK: J9.5 (CLK), U8.15 (PA5), U14.3
TSNS_EXT_ALERT: J2.5, R19.2, U8.13 (PA3)
TSNS_INT_ALERT: R20.2, U8.12 (PA2), U18.3 (Alert)
UART_GPS_MCU: R15.1, U8.31 (PA10)
UART_MCU_GPS: R14.1, U8.30 (PA9)
V-5P0: C79.1, FB4.2, R37.2, R41.2, R56.2, R59.1
V-8P0_PA: C31.1, C81.2, C82.1, FB3.2, L13.1, R57.1

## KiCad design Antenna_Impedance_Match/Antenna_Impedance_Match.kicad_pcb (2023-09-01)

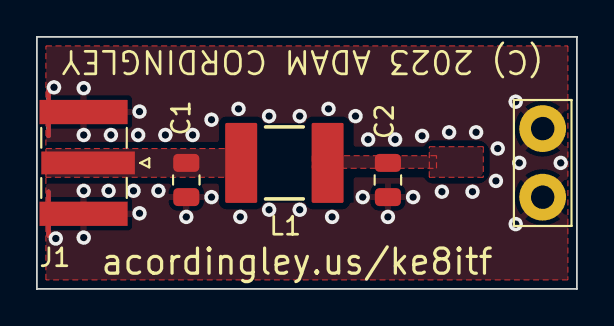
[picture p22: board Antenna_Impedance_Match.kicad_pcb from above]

Board: 2 copper layers, 30.0 x 14.0 mm, 5 parts (0 on the bottom side), 3 nets.

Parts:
C1, C2: 18pF; C_0805_2012Metric
J1: Conn_Coaxial; SMA_Amphenol_132384_EdgeMount
L1: 68nH; L_Coilcraft_1515SQ-68N
TP2: TestPoint; TestPoint_Bridge_Pitch3.81mm_Drill1.3mm

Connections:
/RF_50_SE: C1.2, J1.1 (In), L1.1
/RF_75_SE: C2.2, L1.2
GND: C1.1, C2.1, J1.2 (Ext), TP2.1

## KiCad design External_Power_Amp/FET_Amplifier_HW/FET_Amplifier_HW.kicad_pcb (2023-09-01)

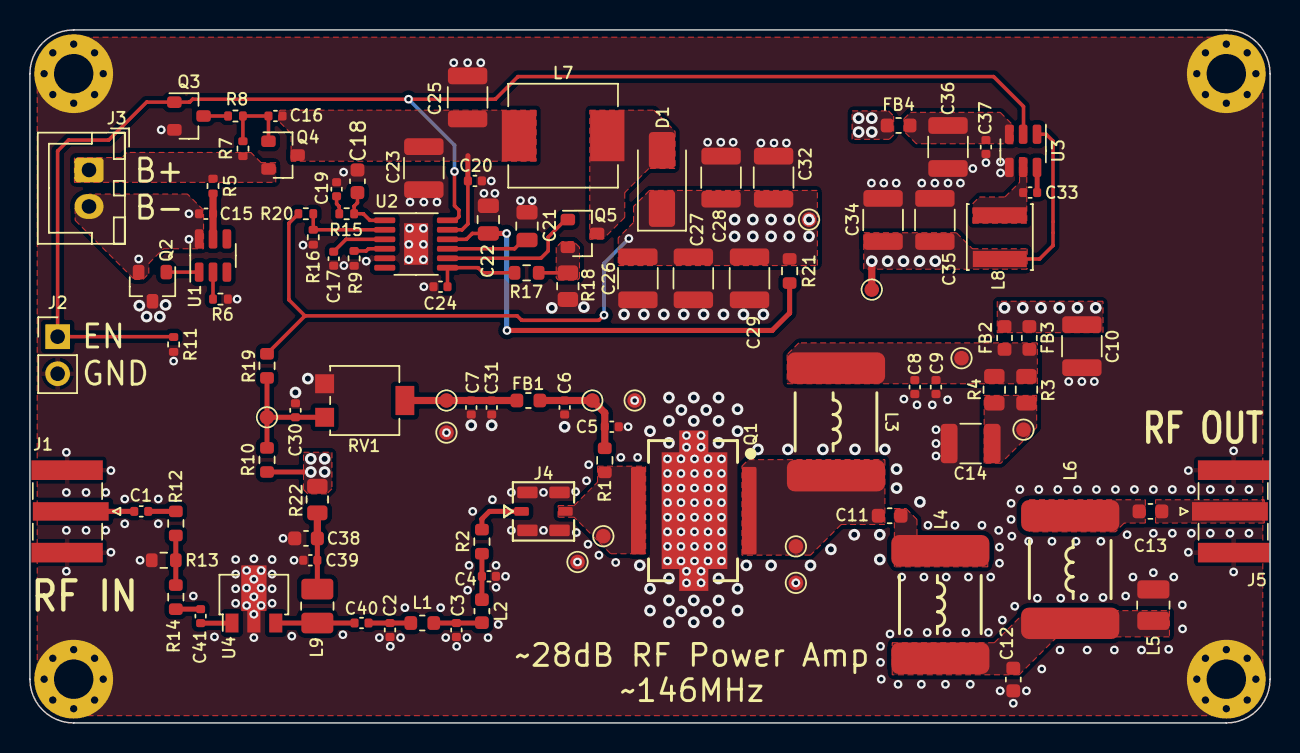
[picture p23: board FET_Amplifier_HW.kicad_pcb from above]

Board: 4 copper layers, 85.0 x 47.5 mm, 110 parts (0 on the bottom side), 49 nets.

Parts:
C1, C5, C8, C16, C24, C31, C39, C40, C41: 1000pF; C_0402_1005Metric
C2: 5.6pF; C_0402_1005Metric
C3: 12pF; C_0402_1005Metric
C4: 3.6pF; C_0402_1005Metric
C6, C7, C9, C15, C17, C20, C30, C33, C37: 0.1uF; C_0402_1005Metric
C10, C14, C36: 10uF; C_1210_3225Metric
C11, C13: 6.8pF; C_0603_1608Metric
C12, C18: 100pF; C_0603_1608Metric
C19: 0.022uF; C_0402_1005Metric
C21: 4.7uF; C_0805_2012Metric
C22: 1uF; C_0805_2012Metric
C23, C25, C26, C27, C28, C29, C32, C34, C35: 22uF; C_1210_3225Metric
C38: 2.2uF; C_0603_1608Metric
D1: SS54SMA; D_SMA
FB1, FB2, FB3, FB4: 330@100MHz; L_0603_1608Metric
H1, H2, H3, H4: M2.5; MountingHole_2.7mm_M2.5_Pad_Via
J1, J5: Conn_Coaxial; SMA_Amphenol_132384_EdgeMount
J2: Conn_01x02; PinHeader_1x02_P2.54mm_Vertical
J3: JST-XH; JST_XH_B2B-XH-A_1x02_P2.50mm_Vertical
J4: MM8430-2610; Connector_Murata_MM8430-2610RA1
L1: 18nH; L_0603_1608Metric
L2: 16nH; L_0603_1608Metric
L3, L4, L6: 180nH; L_Coilcraft_2222SQ-181
L5: 10nH; L_1008_2520Metric
L7: 10uH; L_Sunlord_MWSA0624S
L8: 4.7uH; L_Sunlord_SWPA4018S
L9: 120nH; L_1008_2520Metric_Pad1.43x2.20mm_HandSolder
NT1: NetTie_2; NetTie-2_SMD_Pad0.25mm
Q1: BLP15H9S100GZ; SOT-1483-1
Q2, Q5: DMN3023L; SOT-23
Q3: Si2302; SOT-23
Q4: DMP2035U-7; SOT-23
R1: 49.9; R_0603_1608Metric
R2, R10, R12, R13, R14, R17, R19, R21: 0.0; R_0603_1608Metric
R3, R4: 1.0; R_0805_2012Metric
R5, R8: 330; R_0402_1005Metric
R6: 1k; R_0402_1005Metric
R7, R11, R16: 10k; R_0402_1005Metric
R9: 24.9k; R_0402_1005Metric
R15: 7.5k; R_0402_1005Metric
R18: 0.005; R_0805_2012Metric
R20: 100k; R_0402_1005Metric
R22: 1.8; R_0805_2012Metric
RV1: 10k; Potentiometer_Bourns_3314G_Vertical
TP1, TP2, TP3, TP4, TP5, TP6, TP7, TP8, TP9, TP10, TP11, TP12, TP13: TestPoint; TestPoint_Pad_D1.0mm
U1: AP9101CK6; SOT-23-6
U2: LT3759xMSE; MSOP-12-1EP_3x4mm_P0.65mm_EP1.65x2.85mm
U3: AP63205WU-7; TSOT-23-6
U4: PGA-105; SOT-89-3

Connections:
/BIAS: C7.1, C31.1, FB1.1, RV1.2, TP1.1
/BIAS_FILT: C5.1, C6.1, FB1.2, R1.2, TP2.1
/COAX_TP_IN: J4.1 (IN), R2.2
/C_DAMP: C14.2, R3.2, R4.2, TP7.1
/FET_DRAIN: C11.2, L3.2, Q1.1 (D), TP6.1
/FET_GATE: J4.2 (OUT), Q1.2 (G), R1.1, TP3.1
/FET_PWR_FILT: C8.1, C9.1, FB2.1, FB3.1, L3.1, R3.1, R4.1, TP4.1
/IN_FILT_FINAL: C4.1, L2.2, R2.1
/IN_FILT_LC: C3.1, L1.2, L2.1
/OUT_FILT_1: C11.1, L4.1
/OUT_FILT_2: C12.1, L4.2, L5.1, L6.1
/OUT_FILT_3: C13.2, L6.2
/Power Conversion/BATT_GND: C15.1, J3.2, Q2.2 (S), U1.6 (VSS)
/Power Conversion/BOOST_CS: Q5.2 (S), R17.1, R18.2
/Power Conversion/BOOST_DRV: C22.1, R21.2, U2.10 (DRIVE)
/Power Conversion/BOOST_EN: J2.1, Q3.1 (G), R11.1, U2.12 (EN/UVLO), U3.2 (EN)
/Power Conversion/BOOST_FB: R16.1, R20.1, U2.2 (FBX)
/Power Conversion/BOOST_GATE: Q5.1 (G), U2.8 (GATE)
/Power Conversion/BOOST_ISNS: C24.1, R17.2, U2.7 (SENSE)
/Power Conversion/BOOST_RT: R9.2, U2.4 (RT)
/Power Conversion/BOOST_SS: C17.1, U2.3 (SS)
/Power Conversion/BOOST_SW: D1.2 (A), L7.2, Q5.3 (D)
/Power Conversion/BOOST_VCOMP: C18.1, R15.2, U2.1 (VC)
/Power Conversion/BOOST_VIN: C16.1, C20.2, C23.1, C25.1, L7.1, Q4.3 (D), U2.11 (VIN)
/Power Conversion/BUCK_BST: C33.2, U3.6 (BST)
/Power Conversion/BUCK_FB: NT1.1, U3.1 (FB)
/Power Conversion/BUCK_SW: C33.1, L8.1, U3.5 (SW)
/Power Conversion/BUCK_VIN: C36.2, C37.1, FB4.2, U3.3 (IN)
/Power Conversion/INTVCC: C21.1, U2.9 (INTVCC)
/Power Conversion/PROT_DO: Q2.1 (G), U1.1 (DO)
/Power Conversion/PROT_VDD: C15.2, R5.2, U1.5 (VDD)
/Power Conversion/PROT_VM: R6.1, U1.2 (VM)
/Power Conversion/VC_RC: C19.1, R15.1
/Power Conversion/VIN_EXT: J3.1, Q4.2 (S), R5.1, R7.1
/Power Conversion/VIN_SW_G: C16.2, Q4.1 (G), R7.2, R8.1
/Power Conversion/VIN_SW_NFET_D: Q3.3 (D), R8.2
/RF_AMP_IN: C41.1, U4.1
/RF_AMP_OUT: C40.2, L9.2, U4.3
/RF_IN: C2.1, C40.1, L1.1
/RF_IN_EXT: C1.2, J1.1 (In)
/RF_OUT_EXT: C13.1, J5.1 (In)
/TEE_ATTN: R12.2, R13.2, R14.1
/TEE_ATTN_IN: C1.1, R12.1
/TEE_OUT: C41.2, R14.2
/V-VCC_BIAS: C30.1, R10.1, R19.1, RV1.3, TP9.1
BOOST_VOUT: C10.2, C26.1, C27.1, C28.1, C29.1, C32.1, D1.1 (K), FB2.2, FB3.2, FB4.1, R19.2, R20.2, R21.1, TP5.1
GND: C2.2, C3.2, C4.2, C5.2, C6.2, C7.2, C8.2, C9.2, C10.1, C12.2, C14.1, C17.2, C18.2, C19.2, C20.1, C21.2, C22.2, C23.2, C24.2, C25.2, C26.2, C27.2, C28.2, C29.2, C30.2, C31.2, C32.2, C34.2, C35.2, C36.1, C37.2, C38.2, C39.1, H1.1, H2.1, H3.1, H4.1, J1.2 (Ext), J2.2, J4.3 (GND), J5.2 (Ext), L5.2, Q1.3 (S), Q2.3 (D), Q3.2 (S), R6.2, R9.1, R11.2, R13.1, R16.2, R18.1, RV1.1, TP8.1, TP11.1, TP12.1, TP13.1, U2.5 (SYNC), U2.13 (GND), U3.4 (GND), U4.2 (GND)
unnamed: C38.1, C39.2, L9.1, R22.1
V-5P0: C34.1, C35.1, L8.2, NT1.2, R10.2, R22.2, TP10.1

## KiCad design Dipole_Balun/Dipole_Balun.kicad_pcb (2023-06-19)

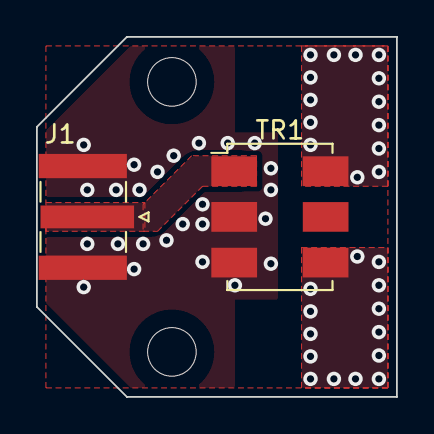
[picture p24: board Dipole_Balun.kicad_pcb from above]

Board: 2 copper layers, 20.0 x 20.0 mm, 4 parts (0 on the bottom side), 2 nets, no tracks yet.

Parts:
H1, H2: M2.5; MountingHole_2.7mm_M2.5
J1: Conn_Coaxial; SMA_Amphenol_132384_EdgeMount
TR1: ADT1.5-1; Mini-Circuits_CD542_H2.84mm

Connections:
/RF_IN: J1.1 (In), TR1.1
GND: J1.2 (Ext), TR1.2, TR1.3

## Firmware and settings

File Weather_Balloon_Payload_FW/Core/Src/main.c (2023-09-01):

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
/* Includes ------------------------------------------------------------------*/
#include "main.h"
#include "dma.h"
#include "fatfs.h"
#include "hrtim.h"
#include "i2c.h"
#include "spi.h"
#include "tim.h"
#include "usart.h"
#include "gpio.h"

/* USER CODE BEGIN Includes */

#include <stdio.h>
#include <string.h>
#include <stdlib.h>
#include <stdbool.h>
#include <stdarg.h> //for va_list var arg functions
#include "adf4002.h"
#include "mcp9808.h"
#include "printf.h"
#include "ublox.h"
#include "ax25.h"
#include "aprs.h"

/* USER CODE END Includes */

/* USER CODE BEGIN PTD */
#define MAX_FILE_COUNT 16

typedef enum radio_mode_enum {
  MODE_MANUAL,
  MODE_AUTO,
  MODE_TEST
}radio_mode_t;

typedef enum radio_states_enum {
  STATE_IDLE,
  STATE_POWER_ON_LO,
  STATE_WAIT_FOR_LO_LOCK,
  STATE_POWER_ON_PA,
  STATE_WAIT_FOR_PA,
  STATE_TRANSMIT,
  STATE_GOTO_IDLE
}radio_state_t;

typedef enum fields_enum {
  MODE,
  RADIO_STATE,
  PA_EN,
  LO_GEN_EN,
  LO_PLL_R_COUNTER_H,
  LO_PLL_R_COUNTER_L,
  LO_PLL_N_COUNTER_H,
  LO_PLL_N_COUNTER_L,
  LO_PLL_LOCK,
  CALLSIGN_0,
  CALLSIGN_1,
  CALLSIGN_2,
  CALLSIGN_3,
  CALLSIGN_4,
  CALLSIGN_5,
  TX_PERIOD_H,
  TX_PERIOD_L,
  LOG_INTERVAL,
  SD_CARD_OK,
  GPS_PPS_OK,
  DEBUG_MODE,
  SEND_PACKET_NOW,
  NUM_FIELDS
}FieldId_t;

typedef struct sd_card_struct {
  FATFS filesys; // fatfs handle
  FRESULT result;
  DWORD free_clusters;
  DWORD free_sectors;
  DWORD total_sectors;
}SdCard_t;
/* USER CODE END PTD */

/* USER CODE BEGIN PD */
#define CMD_NONE        0x00
#define CMD_READ        0x01
#define CMD_READ_BLOCK  0x02
#define CMD_WRITE       0x03
#define CMD_WRITE_BLOCK 0x04
#define CMD_COMMS_TEST  0x05
#define NUM_CMDS        (CMD_COMMS_TEST + 1)
#define CMD_ERROR       0x06

#define START_BYTE  0xA5
#define IND_CMD     1
#define LEN_IND     (IND_CMD + 1)
#define BODY_IND    (LEN_IND + 1)

#define MAX_PACKET_LEN  ((2*NUM_FIELDS) + BODY_IND)
#define UART_STATE_RCV_HDDR   0x00
#define UART_STATE_RCV_BODY   0x01
#define UART_STATE_RCV_ERROR  0x02

#define TX_PERIOD_SECONDS     300

#define PLL_LOCK_DURATION_US  50000

#define STARTUP_DELAY_US      1000000

#define POLL_GPS_INTERVAL     5000

#define TEMPERATURE_INTERVAl  1000000

#define CALLSIGN_LEN          6
#define FILE_CHUNK_SIZE       256
#define DEBUG_LINE_SIZE       128
#define DEBUG_BUF_SIZE        (DEBUG_LINE_SIZE + 20)
#define DEBUG_MODE_NORMAL     0
#define DEBUG_MODE_CONSOLE    1
#define UART_DEBUG_BUF_SIZE   256
#define DEFAULT_MARK_COUNT    2103
#define DEFAULT_SPACE_COUNT   2102

#define FRAME_SIZE_MAX        128
#define SPACE                 0
#define MARK                  1
#define FRAME_DELIM           0x7E

#define APRS_SCRATCH_SIZE     256
#define MAX_APRS_FRAME_COUNT  8

/* USER CODE END PD */


/* USER CODE BEGIN PV */

uint8_t uart_rx_buf[MAX_PACKET_LEN];
volatile uint8_t packet_lock = 0;
uint8_t packet[MAX_PACKET_LEN];
int uart_rx_ind = 0;
uint8_t uart_rx_state = 0;
uint8_t uart_tx_buf[MAX_PACKET_LEN];
bool update_sys = true;

/* field memory for debug interface */
uint8_t field_mem[NUM_FIELDS];
bool field_mem_writable[NUM_FIELDS];

MCP9808_t tsns_on_board;
MCP9808_t tsns_outside;

ADF4002_t lo_gen_pll;

volatile bool startup = true;

volatile uint64_t microseconds = 0;
volatile uint64_t last_pps_timestamp = 0;
volatile uint64_t pps_duration_us = 0;
volatile uint64_t last_tx_timestamp = 0;
volatile uint64_t begin_lock_timestamp = 0;
volatile uint64_t last_log_timestamp = 0;
volatile uint64_t poll_gps_timestamp = 0;
volatile uint64_t gps_microseconds = 0; // the actual count of microseconds according to GPS
volatile int64_t gps_local_discrepancy = 0;

/* SD CARD THINGS */
SdCard_t sdcard;
bool sd_init_success = false;
FIL config_file;

/* GPS THINGS */
MaxM8C_t gps;
FIL gps_logfile;
bool log_gps = false;
gnss_position_t gps_pos;

/* RADIO THINGS */
int hi_rate_period = 5; // period in seconds for high-rate telemetry
uint8_t tx_frame[FRAME_SIZE_MAX];
int tx_frame_len = 0;
int mark_or_space = 0;
int frame_byte_ind = -1;
int frame_bit_ind = 0;
int seq_ones_count = 0;
bool stuff_bit = false;
uint8_t* aprs_scratch[APRS_SCRATCH_SIZE];
Ax25Frame_t* aprs_frames;
int aprs_frame_count = 0;

/* HOUSEKEEPING THINGS */
const char* debug_fname = "debug.txt";
char debug_buf[DEBUG_BUF_SIZE]; // used by the handy dandy debug function
char debug_line[DEBUG_LINE_SIZE]; // used by user (dats me) to snprintf stuff to
char uart_debug_buf[UART_DEBUG_BUF_SIZE];
char uart_scratch_buf[DEBUG_BUF_SIZE];
volatile int uart_debug_buf_pos = 0;
volatile int uart_debug_tx_len = 0;

/* USER CODE END PV */

void SystemClock_Config(void);
/* USER CODE BEGIN PFP */

void init_field_mem(uint8_t * mem, bool * writable);
void strstrip(char* str, char* loc);
void init_field_mem_from_config(uint8_t * mem, SdCard_t* sd, FIL* fp);
uint64_t get_microseconds();
bool init_sdcard(SdCard_t* sdcard);
int file_open_read(SdCard_t* sd, const TCHAR* fname, FIL* fp);
int file_open_write(SdCard_t* sd, const TCHAR* fname, FIL* fp);
void file_append_line(SdCard_t* sd, const TCHAR* fname, char* line);
void stop_fsk_output();
void start_fsk_output();
void set_fsk_freq_mark();
void set_fsk_freq_space();
void debug_all(char* line);
void debug(char* line);
void debug_uart(char* line);
void debug_gps(char* line);

/* USER CODE END PFP */

/**
  * @brief  The application entry point.
  * @retval int
  */
int main(void)
{
  /* MCU Configuration--------------------------------------------------------*/

  /* Reset of all peripherals, Initializes the Flash interface and the Systick. */
  HAL_Init();

  /* Configure the system clock */
  SystemClock_Config();

  /* Initialize all configured peripherals */
  MX_GPIO_Init();
  MX_DMA_Init();
  MX_HRTIM1_Init();
  MX_I2C1_Init();
  MX_SPI1_Init();
  MX_USART1_UART_Init();
  MX_USART3_UART_Init();
  MX_FATFS_Init();
  MX_TIM1_Init();
  MX_TIM2_Init();
  /* USER CODE BEGIN 2 */

  HAL_GPIO_WritePin(SD_CS_GPIO_Port, SD_CS_Pin, 1);

  // turn off RF amp power supplies
  HAL_GPIO_WritePin(EN_5P0_GPIO_Port, EN_5P0_Pin, 0);
  HAL_GPIO_WritePin(PA_EN_GPIO_Port, PA_EN_Pin, 0);

  // chip select lines high
  HAL_GPIO_WritePin(PLL_LE_GPIO_Port, PLL_LE_Pin, 0);
  HAL_GPIO_WritePin(SD_CS_GPIO_Port, SD_CS_Pin, 1);

  init_field_mem(field_mem, field_mem_writable);

  lo_gen_pll.hspi = &hspi1;
  lo_gen_pll.ce_pin = PLL_CE_Pin;
  lo_gen_pll.ce_port = PLL_CE_GPIO_Port;
  lo_gen_pll.le_pin = PLL_LE_Pin;
  lo_gen_pll.le_port = PLL_LE_GPIO_Port;
  adf_disable_chip(&lo_gen_pll);
  adf_init_mem(&lo_gen_pll);
  adf_set_n_counter(&lo_gen_pll, 1422, false);
  adf_set_r_counter(&lo_gen_pll, 120, false);
  adf_init_chip(&lo_gen_pll);
  adf_disable_chip(&lo_gen_pll);

  // begin receiveing stuff from Debug port
  HAL_UART_Receive_DMA(&huart3, uart_rx_buf + uart_rx_ind, BODY_IND); 

  // start 10kHz clock
  HAL_TIM_Base_Start_IT(&htim2);
  
  // Init GPS Receiver
  gps.delay_ms = HAL_Delay;
  gps.console_print = debug_uart;
  ublox_init(&gps, &hi2c1, &huart1, GPS_RESETB_GPIO_Port, GPS_RESETB_Pin);
  ublox_hw_reset(&gps);
  HAL_Delay(500);
  ublox_config_i2c(&gps);
  ublox_config_gnss(&gps);
  HAL_Delay(500);
  ublox_enable_inf_messages(&gps);
  ublox_enable_utc_time_messages(&gps);
  ublox_enable_pvt_messages(&gps);
  ublox_enable_nav_messages(&gps);

  /* Temperature sensor things */
  tsns_on_board.hi2c = &hi2c1;
  tsns_on_board.i2c_addr = 0x30; // already left-shifted
  tsns_on_board.online = true;

  tsns_outside.hi2c = &hi2c1;
  tsns_outside.i2c_addr = 0x32; // already left-shifted
  tsns_outside.online = true;

  /* USER CODE END 2 */

  /* Infinite loop */
  /* USER CODE BEGIN WHILE */
  while (1)
  {
    /* USER CODE END WHILE */

    /* USER CODE BEGIN 3 */

    /* BEGIN PROCESSING DEBUG PACKET */
    if(packet_lock > 0){
      // process the packet

      // sanity check
      if(packet[0] == START_BYTE){
        uart_tx_buf[0] = START_BYTE;
        uart_tx_buf[IND_CMD] = packet[IND_CMD];
        switch(packet[IND_CMD]){
          case CMD_NONE:{
            // EZ clap
            break;
          }
          case CMD_READ:{
            // body is a list of indices 
            uint8_t* tx_body = uart_tx_buf + BODY_IND;
            int tx_body_ind = 0;
            for(int i = 0; i < packet[BODY_IND]; i++){
              tx_body[tx_body_ind] = packet[i]; // copy field id
              tx_body_ind++;
              tx_body[tx_body_ind] = field_mem[packet[i]]; // copy actual data
              tx_body_ind++;
            }
            uart_tx_buf[LEN_IND] = tx_body_ind;
            break;
          }
          case CMD_READ_BLOCK:{
            // body is a start index and a length
            uint8_t block_start = packet[BODY_IND];
            uint8_t block_len = packet[BODY_IND + 1];
            if(block_len > NUM_FIELDS - block_start){
              if(NUM_FIELDS - block_start < 0){
                block_len = 0;
              }else{
                block_len = NUM_FIELDS - block_start;
              }
            }

            // copy from field memory
            memcpy(uart_tx_buf + BODY_IND, field_mem + block_start, block_len);

            break;
          }
          case CMD_WRITE:{
            // body is a list of id:value pairs
            uint8_t* rx_body = packet + BODY_IND;
            uint8_t* tx_body = uart_tx_buf + BODY_IND;
            int rx_body_ind = 0;
            int tx_body_ind = 0;
            for(int i = 0; i < packet[LEN_IND]; i++){
              uint8_t field_id = rx_body[i];
              i++;
              if(field_mem_writable[field_id]){
                field_mem[field_id] = rx_body[i];
                tx_body[tx_body_ind] = field_id;
                tx_body_ind++;
              }
            }
            uart_tx_buf[LEN_IND] = tx_body_ind;
            if(tx_body_ind > 0){
              update_sys = true;
            }
            break;
          }
          case CMD_WRITE_BLOCK:{
            // body is a start id + block of data
            uint8_t block_start = packet[BODY_IND];
            uint8_t block_len = packet[LEN_IND] - 1;
            if(block_len > NUM_FIELDS - block_start){
              if(NUM_FIELDS - block_start < 0){
                block_len = 0;
              }else{
                block_len = NUM_FIELDS - block_start;
              }
            }
            uint8_t* block = packet + BODY_IND + 1;
            int field_id = block_start;
            uint8_t updated_len = 0;
            for(int i = 0; i < block_len; i++){
              if(field_mem_writable[field_id]){
                field_mem[field_id] = block[i];
                updated_len++;
              }
              field_id++;
            }
            uart_tx_buf[LEN_IND] = 1;
            uart_tx_buf[BODY_IND] = updated_len;
            if(updated_len > 0){
              update_sys = true;
            }
            break;
          }
          case CMD_COMMS_TEST:{
            uart_tx_buf[LEN_IND] = 4;
            uart_tx_buf[BODY_IND] = packet[BODY_IND];
            uart_tx_buf[BODY_IND+1] = packet[BODY_IND+1];
            uart_tx_buf[BODY_IND+2] = packet[BODY_IND+2];
            uart_tx_buf[BODY_IND+3] = packet[BODY_IND+3];
            // nothing else to do, just send empty packet
          }
        }

        packet_lock = 0; // release lock so we can receive new data

        // transmit
        HAL_UART_Transmit_DMA(&huart3, uart_tx_buf, BODY_IND + uart_tx_buf[LEN_IND]);
      }
      
    }
    /* END PROCESSING DEBUG PACKET */
    
    /* BEGIN CHECKING FOR FIELD MEM UPDATES */
    if(update_sys){
      if(field_mem[MODE] == MODE_MANUAL){
        if(field_mem[LO_GEN_EN]){
          uint16_t r_value = (field_mem[LO_PLL_R_COUNTER_H] << 8) | field_mem[LO_PLL_R_COUNTER_L];
          uint16_t n_value = (field_mem[LO_PLL_N_COUNTER_H] << 8) | field_mem[LO_PLL_N_COUNTER_L];
          adf_set_r_counter(&lo_gen_pll, r_value, true);
          adf_set_n_counter(&lo_gen_pll, n_value, true);
          adf_enable_chip(&lo_gen_pll);
          HAL_GPIO_WritePin(EN_5P0_GPIO_Port, EN_5P0_Pin, 1); // enable misc RF amps and such
        }else{
          adf_disable_chip(&lo_gen_pll);
          HAL_GPIO_WritePin(EN_5P0_GPIO_Port, EN_5P0_Pin, 0); // enable misc RF amps and such
        }
        if(field_mem[PA_EN]){
          HAL_GPIO_WritePin(PA_EN_GPIO_Port, PA_EN_Pin, 1); // enable misc RF amps and such
        }else{
          HAL_GPIO_WritePin(PA_EN_GPIO_Port, PA_EN_Pin, 0); // enable misc RF amps and such
        }
        
        if(field_mem[SEND_PACKET_NOW]){
          set_fsk_freq_mark();
          start_fsk_output();
        }else{
          stop_fsk_output();
        }
        
      }
      update_sys = false;
    }
    /* END CHECKING FOR FIELD MEM UPDATES */

    /* BEGIN CHECKING GPS LOCK */
    // check for PPS presence
    if (pps_duration_us == 0 ||
        get_microseconds() > (last_pps_timestamp + pps_duration_us + 2500) ){
      // we don't have GPS signal
      if(field_mem[GPS_PPS_OK]){
        debug_all("GPS PPS not present/lost");
        debug_all("");
      }
      field_mem[GPS_PPS_OK] = false;
      HAL_GPIO_WritePin(LED_0_GPIO_Port, LED_0_Pin, 0);
    }else{
      // we have a GPS signal!
      if(!field_mem[GPS_PPS_OK]){
        gps_microseconds = get_microseconds(); // start gps counter in agreement with XO
        debug_all("GPS PPS present");
      }
      field_mem[GPS_PPS_OK] = true;
      HAL_GPIO_WritePin(LED_0_GPIO_Port, LED_0_Pin, 1);
    }
    /* END GPS LOCK CHECKING */

    /* BEGIN STARTUP DELAY CHECKING */
    if(startup && get_microseconds() > STARTUP_DELAY_US){
      if(HAL_GPIO_ReadPin(SD_DET_GPIO_Port, SD_DET_Pin) == 0){
        // an SD card is inserted
        // attempt to initialize the SD card
        debug_all("Attempting to intialize SD card...");
        field_mem[SD_CARD_OK] = init_sdcard(&sdcard);
      }
      if(field_mem[SD_CARD_OK]){
        // read config parameters from sd card
        if(file_open_read(&sdcard, "config.txt", &config_file) == 0){
          debug_all("Initializing fields from SD card...");
          init_field_mem_from_config(field_mem, &sdcard, &config_file);
          update_sys = true;
          f_close(&config_file);
        }

        // attempt to open GPS log file
        if((log_gps = (file_open_write(&sdcard, UBLOX_LOG_FILENAME, &gps_logfile) == 0))){
          f_close(&gps_logfile); // close until we need it
        }
      }else{
        debug_all("SD card init failed...");
      }
      startup = false;
    }
    /* END STARTUP DELAY CHECKING */


    /* BEGIN GPS DATA GRAB AND LOGGING */
    if(get_microseconds() - poll_gps_timestamp > POLL_GPS_INTERVAL){
      // debug_all("Polling GPS...");
      poll_gps_timestamp = get_microseconds();
      int avail = ublox_bytes_available_i2c(&gps);
      if(avail > 0){
        // snprintf(debug_line, DEBUG_LINE_SIZE, "GPS bytes available: %d", avail);
        // debug_all(debug_line);
        // HAL_Delay(10);
        ublox_read_all_data_i2c(&gps, 0);
        ublox_parse_messages(&gps);
        ublox_print_all_messages(&gps, debug_all); //debug_line);
        // // debug_all(debug_line);

        // TODO do real things with the GPS messages 
        for(int i = 0; i < gps.msg_count; i++){
          ubx_msg_t* msg = gps.msgs + i;
          if(msg->class == UBX_NAV_CLASS){
            
            if(msg->id == 0x21){
              // UBX-NAV-TIMEUTC
              gnss_timestamp_t* ts = &(gps.ts);
              ublox_get_gnss_timestamp(msg->payload, ts);
              // TODO packetize and all that
            }else if(msg->id == 0x14){
              // UBX-NAV-HPPOSLLH
              ublox_parse_hpposllh(msg, &gps_pos);
              
            }
          }
        }

        ublox_cleanup_messages(&gps);

        ublox_poll_message_i2c(&gps, UBX_NAV_CLASS, 0x35); // poll satellite information
        HAL_Delay(10);

        ublox_read_all_data_i2c(&gps, 0);
        ublox_parse_messages(&gps);
        ublox_print_all_messages(&gps, debug_all); //debug_line);
        ublox_cleanup_messages(&gps);
      }else if(avail < 0){
        // debug_all("GPS likely offline.");
      }
      
      
    }

    // write generic data to the log file
    if(get_microseconds() - last_log_timestamp > (field_mem[LOG_INTERVAL] * 1000000)){
      last_log_timestamp = get_microseconds();
    }
    /* END GPS DATA GRAB AND LOGGING */

    /* BEGIN TEMPERATURE AND BAROMETRIC PRESSURE DATA GRAB */
    if( (tsns_on_board.online && get_microseconds() - tsns_on_board.update_ts > TEMPERATURE_INTERVAl) || 
        (!tsns_on_board.online && get_microseconds() - tsns_on_board.update_ts > 10*TEMPERATURE_INTERVAl)
    ){
      mcp9808_get_temperature(&tsns_on_board);
      tsns_on_board.update_ts = get_microseconds();
      if(!tsns_on_board.online){
        debug_all("On-board temp sensor offline :(");
      }else{
        // snprintf(debug_line, DEBUG_LINE_SIZE, "(T-ONBOARD) %.2f°C", tsns_on_board.temp);
        // debug_all(debug_line);
      }
    }
    if( (tsns_outside.online && get_microseconds() - tsns_outside.update_ts > TEMPERATURE_INTERVAl) || 
        (!tsns_outside.online && get_microseconds() - tsns_outside.update_ts > 10*TEMPERATURE_INTERVAl)
    ){
      mcp9808_get_temperature(&tsns_outside);
      tsns_outside.update_ts = get_microseconds();
      if(!tsns_outside.online){
        debug_all("Outside temp sensor offline :(");
      }else{
        // snprintf(debug_line, DEBUG_LINE_SIZE, "(T-OUTSIDE) %.2f°C", tsns_outside.temp);
        // debug_all(debug_line);
      }
    }
    
    /* END TEMPERATURE AND BAROMETRIC PRESSURE DATA GRAB */

    /* BEGIN FORMING APRS PACKETS */
    uint64_t elapsed_us = get_microseconds() - last_tx_timestamp;
    uint16_t tx_period = (field_mem[TX_PERIOD_H] << 8) | field_mem[TX_PERIOD_L];
    if ((elapsed_us / 1000000) >= tx_period){
      // 
      debug_all("Forming APRS packet...");
      int offset = 0;
      /* LAT/LONG POSITION REPORT */
      /* with timestamp, with APRS messaging, zulu time, with comment */
      offset += snprintf(aprs_scratch + offset, APRS_SCRATCH_SIZE - offset, "%c", APRS_POS_WITH_TS_MSG);

      /* append UTC timestamp (zulu time) */
      offset += snprintf(aprs_scratch + offset, APRS_SCRATCH_SIZE - offset, "%02d%02d%02dz", gps.ts.day, gps.ts.hour, gps.ts.minute);

      /* append latitude */
      int lat_degrees = (int)gps_pos.lat; 
      float lat_minutes = (gps_pos.lat - 1.0*lat_degrees)*60.0; // 60 minutes per degree
      char n_or_s = (lat_degrees > 0 ? 'N' : 'S');
      char symbol_table_id = '/'; // primary symbol table
      offset += snprintf(aprs_scratch + offset, APRS_SCRATCH_SIZE - offset, "%02d%05.2f%c%c", lat_degrees, lat_minutes, n_or_s, symbol_table_id);

      /* append longitude */
      int lon_degrees = (int)gps_pos.lon; 
      float gps_lon_dec = gps_pos.lon;
      char w_or_e = 'E';
      if(lon_degrees < 0){
        lon_degrees = 0 - lon_degrees;
        gps_lon_dec = 0.0 - gps_lon_dec;
        w_or_e = 'W';
      }
      float lon_minutes = (gps_lon_dec - 1.0*lon_degrees)*60.0; // 60 minutes per degree
      char symbol_code = 'O'; // balloon
      offset += snprintf(aprs_scratch + offset, APRS_SCRATCH_SIZE - offset, "%02d%05.2f%c%c", lon_degrees, lon_minutes, w_or_e, symbol_code);

      /* append comment */
      int alt_ft = (int)(gps_pos.altitude * 3.2808);
      char* comment = "Test";
      offset += snprintf(aprs_scratch + offset, APRS_SCRATCH_SIZE - offset, "%s /A=%06d", comment, alt_ft);

      debug_all(aprs_scratch);
    }
    /* END FORMING APRS PACKETS */
  }
  /* USER CODE END 3 */
}

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
/* USER CODE BEGIN 4 */

void init_field_mem(uint8_t * mem, bool* writable){
  memset(writable, 0x00, NUM_FIELDS);
  memset(mem, 0x00, NUM_FIELDS);
  mem[MODE] = MODE_MANUAL;
  writable[MODE] = true;

  mem[RADIO_STATE] = STATE_GOTO_IDLE;
  writable[RADIO_STATE] = true; // may want to change this later

  mem[PA_EN] = 0;
  writable[PA_EN] = true;

  mem[LO_GEN_EN] = 0;
  writable[LO_GEN_EN] = true;

  mem[LO_PLL_R_COUNTER_H] = 0;
  writable[LO_PLL_R_COUNTER_H] = true;
  mem[LO_PLL_R_COUNTER_L] = 120;
  writable[LO_PLL_R_COUNTER_L] = true;

  mem[LO_PLL_N_COUNTER_H] = (1422 >> 8) & 0xFF;
  writable[LO_PLL_N_COUNTER_H] = true;
  mem[LO_PLL_N_COUNTER_L] = (1422 & 0xFF);
  writable[LO_PLL_N_COUNTER_L] = true;
  
  mem[CALLSIGN_0] = 'K';
  writable[CALLSIGN_0] = true;
  mem[CALLSIGN_1] = 'E';
  writable[CALLSIGN_1] = true;
  mem[CALLSIGN_2] = '8';
  writable[CALLSIGN_2] = true;
  mem[CALLSIGN_3] = 'I';
  writable[CALLSIGN_3] = true;
  mem[CALLSIGN_4] = 'T';
  writable[CALLSIGN_4] = true;
  mem[CALLSIGN_5] = 'F';
  writable[CALLSIGN_5] = true;

  mem[LOG_INTERVAL] = 5;
  writable[LOG_INTERVAL] = true;

  mem[TX_PERIOD_H] = (TX_PERIOD_SECONDS >> 8) & 0xFF;
  writable[TX_PERIOD_H] = true;
  mem[TX_PERIOD_L] = TX_PERIOD_SECONDS & 0xFF;
  writable[TX_PERIOD_L] = true;

  mem[SD_CARD_OK] = false; // default to this
  mem[GPS_PPS_OK] = false; // default

  mem[DEBUG_MODE] = DEBUG_MODE_NORMAL;
  writable[DEBUG_MODE] = true;

  mem[SEND_PACKET_NOW] = 0;
  writable[SEND_PACKET_NOW] = true;

  // populate the tx_frame with our callsign
  tx_frame_len = 7;
  for(int i = 0; i < tx_frame_len; i++){
    tx_frame[i] = mem[CALLSIGN_0 + i];
  }
  tx_frame[6] = ' ';
} 


/**
 * strip whitespace from str storing result in loc
 * loc must have at least as much space as str
*/
void strstrip(char* str, char* loc){
  int i = 0;
  while(str[i] == ' ' || str[i] == '\n' || str[i] == '\r' || str[i] == '\t'){
    i++;
  }
  strcpy(loc, str + i); // copy over everything except leading whitespace

  i = strlen(loc) - 1; // get index of last character
  while(i >= 0 && (loc[i] == ' ' || loc[i] == '\n' || loc[i] == '\r' || loc[i] == '\t')){
    loc[i] = '\0'; // set this whitespace to null termination
    i--;
  }
}
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

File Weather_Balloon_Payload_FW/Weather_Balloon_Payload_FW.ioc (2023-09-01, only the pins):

Mcu.UserName=STM32F334C8Tx
PA0.GPIO_Label=GPS_PPS
PA0.Signal=GPXTI0
PA1.GPIO_Label=GPS_EXTINT
PA1.Signal=GPXTI1
PA10.Signal=USART1_RX
PA13.Signal=SYS_JTMS-SWDIO
PA14.Signal=SYS_JTCK-SWCLK
PA2.GPIO_Label=TSENS_INT_ALERT
PA2.Signal=GPXTI2
PA3.GPIO_Label=TSNS_EXT_ALERT
PA3.Signal=GPXTI3
PA4.GPIO_Label=PLL_LE
PA4.Signal=GPIO_Output
PA5.Signal=SPI1_SCK
PA6.Signal=SPI1_MISO
PA7.Signal=SPI1_MOSI
PA8.Signal=RCC_MCO
PA9.Signal=USART1_TX
PB0.GPIO_Label=GPS_RESETB
PB0.Signal=GPIO_Output
PB1.GPIO_Label=PLL_CE
PB1.Signal=GPIO_Output
PB10.Signal=USART3_TX
PB11.Signal=USART3_RX
PB12.Signal=HRTIM1_CHC1
PB13.GPIO_Label=LED_0
PB13.Signal=GPIO_Output
PB14.GPIO_Label=LED_1
PB14.Signal=GPIO_Output
PB15.GPIO_Label=LED_2
PB15.Signal=GPIO_Output
PB2.GPIO_Label=SD_CS
PB2.Signal=GPIO_Output
PB3.GPIO_Label=PA_EN
PB3.Signal=GPIO_Output
PB4.GPIO_Label=EN_5P0
PB4.Signal=GPIO_Output
PB5.GPIO_Label=PLL_MUXOUT
PB5.Signal=GPIO_Input
PB6.Signal=I2C1_SCL
PB7.Signal=I2C1_SDA
PB8.GPIO_Label=SD_DET
PB8.Signal=GPIO_Input
PB9.GPIO_Label=BUZZ_LED_EN
PB9.Signal=GPIO_Output

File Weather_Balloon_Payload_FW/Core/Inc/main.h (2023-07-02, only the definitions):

#define GPS_PPS_Pin GPIO_PIN_0
#define GPS_PPS_GPIO_Port GPIOA
#define GPS_PPS_EXTI_IRQn EXTI0_IRQn
#define GPS_EXTINT_Pin GPIO_PIN_1
#define GPS_EXTINT_GPIO_Port GPIOA
#define GPS_EXTINT_EXTI_IRQn EXTI1_IRQn
#define TSENS_INT_ALERT_Pin GPIO_PIN_2
#define TSENS_INT_ALERT_GPIO_Port GPIOA
#define TSENS_INT_ALERT_EXTI_IRQn EXTI2_TSC_IRQn
#define TSNS_EXT_ALERT_Pin GPIO_PIN_3
#define TSNS_EXT_ALERT_GPIO_Port GPIOA
#define TSNS_EXT_ALERT_EXTI_IRQn EXTI3_IRQn
#define PLL_LE_Pin GPIO_PIN_4
#define PLL_LE_GPIO_Port GPIOA
#define GPS_RESETB_Pin GPIO_PIN_0
#define GPS_RESETB_GPIO_Port GPIOB
#define PLL_CE_Pin GPIO_PIN_1
#define PLL_CE_GPIO_Port GPIOB
#define SD_CS_Pin GPIO_PIN_2
#define SD_CS_GPIO_Port GPIOB
#define LED_0_Pin GPIO_PIN_13
#define LED_0_GPIO_Port GPIOB
#define LED_1_Pin GPIO_PIN_14
#define LED_1_GPIO_Port GPIOB
#define LED_2_Pin GPIO_PIN_15
#define LED_2_GPIO_Port GPIOB
#define PA_EN_Pin GPIO_PIN_3
#define PA_EN_GPIO_Port GPIOB
#define EN_5P0_Pin GPIO_PIN_4
#define EN_5P0_GPIO_Port GPIOB
#define PLL_MUXOUT_Pin GPIO_PIN_5
#define PLL_MUXOUT_GPIO_Port GPIOB
#define SD_DET_Pin GPIO_PIN_8
#define SD_DET_GPIO_Port GPIOB
#define BUZZ_LED_EN_Pin GPIO_PIN_9
#define BUZZ_LED_EN_GPIO_Port GPIOB
#define SD_SPI_HANDLE hspi1

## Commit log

2023-06-19 Update README, block diagrams, schem. Begin layout
    [GPS_and_Barometer.kicad_sch, LO_gen.kicad_sch, Weather_Balloon_Payload_HW.kicad_pcb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]
2023-06-25 Add fabrication files
    [GPS_and_Barometer.kicad_sch, LO_gen.kicad_sch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]
2023-07-02 Antenna imped match files, boilerplate STM code
    [Antenna_Impedance_Match.kicad_pcb, Antenna_Impedance_Match.kicad_sch, GPS_and_Barometer.kicad_sch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]
2023-07-04 Clean up files, add much new code
    [config.txt]
2023-09-01 More work, esp on firmware
    [18650_Battery_Case_1s1p.stl, 18650_battery_case_bottom.stl, AA_Battery_Case_2s2p.stl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]

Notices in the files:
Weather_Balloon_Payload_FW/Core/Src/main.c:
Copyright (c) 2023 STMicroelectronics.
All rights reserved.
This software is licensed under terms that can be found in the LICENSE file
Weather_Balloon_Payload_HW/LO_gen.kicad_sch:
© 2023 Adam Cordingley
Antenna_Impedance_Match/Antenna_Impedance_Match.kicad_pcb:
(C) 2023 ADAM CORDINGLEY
